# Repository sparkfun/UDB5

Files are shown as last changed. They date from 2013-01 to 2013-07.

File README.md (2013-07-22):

UDB5 - UAV Development Board
===============

[UDB5  
*UDB5 (GPS-11703)*](https://www.sparkfun.com/products/11703)

The UDB5 is the fith generation UAV Development board. The main difference from UDB4 is that we moved to an MPU-6000 for the accelerometer and gyro.

For information on the codebase see the [gentlenav repository](https://code.google.com/p/gentlenav/) on google code. 

Repository Contents
-------------------

* **/hardware** - Eagle PCB layout files

License Information
-------------------

All contents of this repository are released under [Creative Commons Share-alike 3.0](http://creativecommons.org/licenses/by-sa/3.0/).

Authors: Jordan McConnell, Aaron Weiss @ SparkFun Electonics

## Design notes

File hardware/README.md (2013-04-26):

UDB5
====

These are the Eagle CAD files for the UDB5.

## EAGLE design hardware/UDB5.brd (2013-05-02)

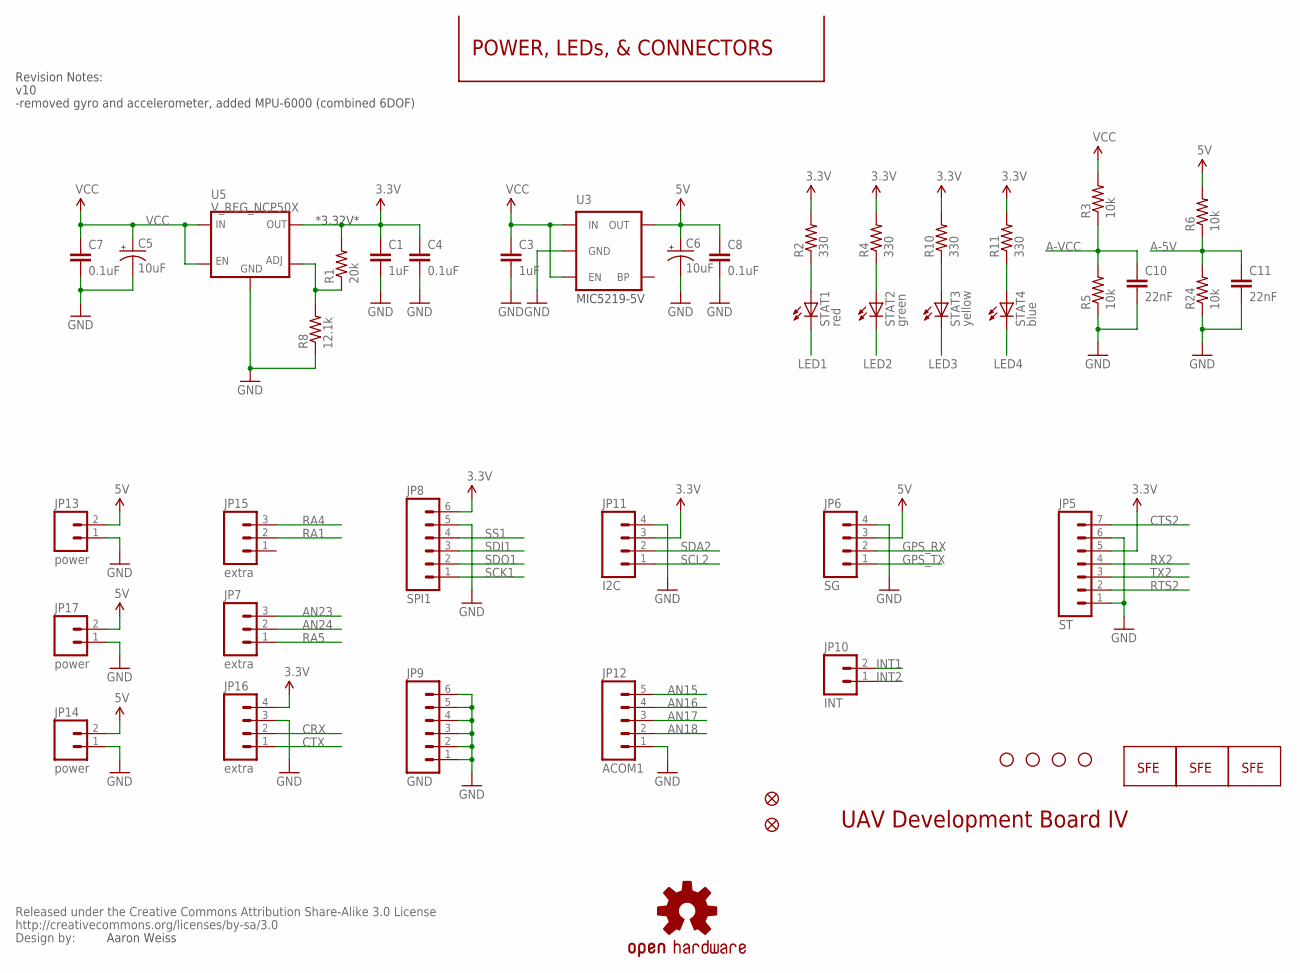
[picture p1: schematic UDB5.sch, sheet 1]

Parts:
C1, C3: 1uF; 0402-CAP
C4, C7, C8: 0.1uF; 0402-CAP
C5, C6: 10uF; EIA3216
C10, C11: 22nF; 0402-CAP
CC_TEXT1: CREATIVE_COMMONS
JP3: LOGO-SFENEW; SFE-NEW-WEBLOGO
JP5: ST; 1X07
JP6: SG; 1X04
JP7, JP15: extra; 1X03
JP8: SPI1; 1X06
JP9: GND; 1X06
JP10: INT; 1X02
JP11: I2C; 1X04
JP12: ACOM1; 1X05
JP13, JP14, JP17: power; 1X02
JP16: extra; 1X04
JP18, JP19: FIDUCIAL1X2.5; FIDUCIAL-1X2.5
LOGO1: LOGO-SFENW2; SFE-NEW-WEB
R1: 20k; 0402-RES
R2, R4, R10, R11: 330; 0402-RES
R3, R5, R6, R24: 10k; 0402-RES
R8: 12.1k; 0402-RES
STAT1: red; LED-0603
STAT2: green; LED-0603
STAT3: yellow; LED-0603
STAT4: blue; LED-0603
U3: V_REG_LDOSMD; SOT23-5
U5: V_REG_NCP50X; DPAK-5
U$2, U$3, U$4, U$5: STAND-OFF
U$9: OSHW-LOGOS; OSHW-LOGO-S
U$10: LOGO-SFESK; SFE-LOGO-FLAME

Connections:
3.3V: C1.1, C4.1, JP5.5, JP8.6, JP11.3, JP16.4, R1.2, R2.2, R4.2, R10.2, R11.2, U5.VOUT (OUT); also elsewhere on the board
5V: C6.A (+), C8.1, JP6.3, JP13.2, JP14.2, JP17.2, R6.2, U3.5 (OUT); also elsewhere on the board
A-5V: C11.1, R6.1, R24.2; also elsewhere on the board
A-VCC: C10.1, R3.1, R5.2; also elsewhere on the board
AN15: JP12.5; also elsewhere on the board
AN16: JP12.4; also elsewhere on the board
AN17: JP12.3; also elsewhere on the board
AN18: JP12.2; also elsewhere on the board
AN23: JP7.3; also elsewhere on the board
AN24: JP7.2; also elsewhere on the board
CRX: JP16.2; also elsewhere on the board
CTS2: JP5.7; also elsewhere on the board
CTX: JP16.1; also elsewhere on the board
GND: C1.2, C3.2, C4.2, C5.C (-), C6.C (-), C7.2, C8.2, C10.2, C11.2, JP5.1, JP5.6, JP6.4, JP8.5, JP9.1, JP9.2, JP9.3, JP9.4, JP9.5, JP9.6, JP11.4, JP12.1, JP13.1, JP14.1, JP16.3, JP17.1, R5.1, R8.1, R24.1, U3.2 (GND), U5.GND; also elsewhere on the board
GPS_RX: JP6.2; also elsewhere on the board
GPS_TX: JP6.1; also elsewhere on the board
INT1: JP10.2; also elsewhere on the board
INT2: JP10.1; also elsewhere on the board
LED1: STAT1.C; also elsewhere on the board
LED2: STAT2.C; also elsewhere on the board
LED3: STAT3.C; also elsewhere on the board
LED4: STAT4.C; also elsewhere on the board
unnamed: R2.1, STAT1.A
unnamed: R4.1, STAT2.A
unnamed: R1.1, R8.2, U5.ADJ
unnamed: R10.1, STAT3.A
unnamed: R11.1, STAT4.A
RA1: JP15.2; also elsewhere on the board
RA4: JP15.3; also elsewhere on the board
RA5: JP7.1; also elsewhere on the board
RTS2: JP5.2; also elsewhere on the board
RX2: JP5.4; also elsewhere on the board
SCK1: JP8.1; also elsewhere on the board
SCL2: JP11.1; also elsewhere on the board
SDA2: JP11.2; also elsewhere on the board
SDI1: JP8.3; also elsewhere on the board
SDO1: JP8.2; also elsewhere on the board
SS1: JP8.4; also elsewhere on the board
TX2: JP5.3; also elsewhere on the board
VCC: C3.1, C5.A (+), C7.1, R3.2, U3.1 (IN), U3.3 (EN), U5.EN, U5.VIN (IN); also elsewhere on the board

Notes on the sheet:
Aaron Weiss
POWER, LEDs, & CONNECTORS
UAV Development Board IV
*3.32V*
MIC5219-5V
v10
-removed gyro and accelerometer, added MPU-6000 (combined 6DOF)
Revision Notes:

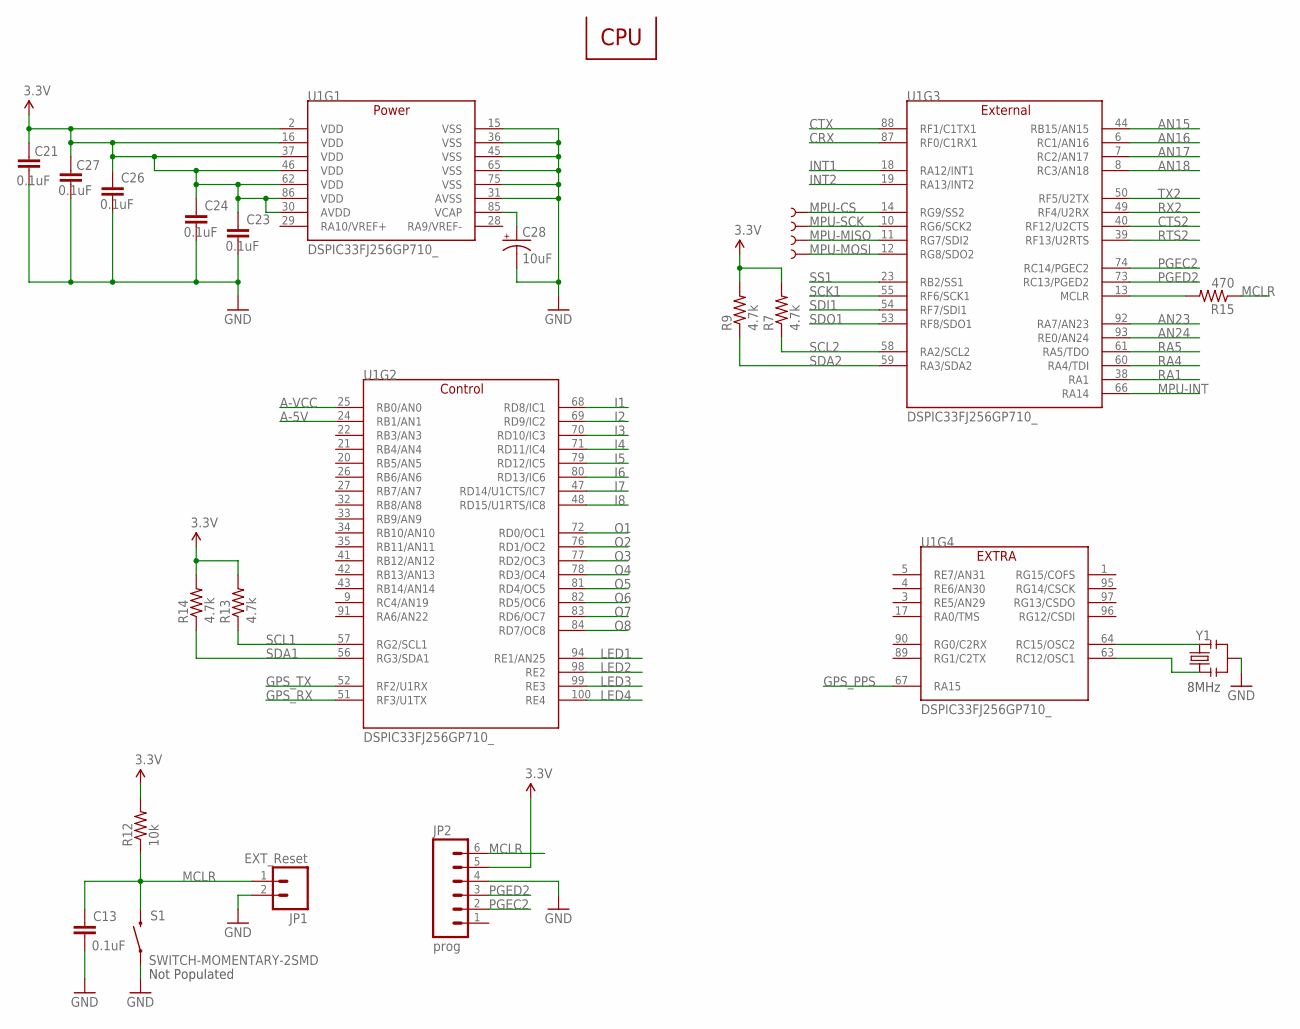
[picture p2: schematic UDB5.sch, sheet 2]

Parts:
C13, C21, C23, C24, C26, C27: 0.1uF; 0402-CAP
C28: 10uF; EIA3216
JP1: EXT_Reset; 1X02
JP2: prog; 1X06
R7, R9, R13, R14: 4.7k; 0402-RES
R12: 10k; 0402-RES
R15: 470; 0402-RES
S1: SWITCH-MOMENTARY-2SMD; TACTILE_SWITCH_SMD
TP1, TP2, TP3, TP4: TEST-POINT3; PAD.03X.03
U1: DSPIC33FJ256GP710_; TQFP-100-12X12MM
Y1: RESONATORSMD; RESONATOR-SMD

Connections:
3.3V: C21.1, C23.1, C24.1, C26.1, C27.1, JP2.5, R7.2, R9.2, R12.2, R13.2, R14.2, U1.2 (VDD), U1.16 (VDD), U1.30 (AVDD), U1.37 (VDD), U1.46 (VDD), U1.62 (VDD), U1.86 (VDD); also elsewhere on the board
A-5V: U1.24 (RB1/AN1); also elsewhere on the board
A-VCC: U1.25 (RB0/AN0); also elsewhere on the board
AN15: U1.44 (RB15/AN15); also elsewhere on the board
AN16: U1.6 (RC1/AN16); also elsewhere on the board
AN17: U1.7 (RC2/AN17); also elsewhere on the board
AN18: U1.8 (RC3/AN18); also elsewhere on the board
AN23: U1.92 (RA7/AN23); also elsewhere on the board
AN24: U1.93 (RE0/AN24); also elsewhere on the board
CRX: U1.87 (RF0/C1RX1); also elsewhere on the board
CTS2: U1.40 (RF12/U2CTS); also elsewhere on the board
CTX: U1.88 (RF1/C1TX1); also elsewhere on the board
GND: C13.2, C21.2, C23.2, C24.2, C26.2, C27.2, C28.C (-), JP1.2, JP2.4, S1.1, U1.15 (VSS), U1.31 (AVSS), U1.36 (VSS), U1.45 (VSS), U1.65 (VSS), U1.75 (VSS), Y1.2; also elsewhere on the board
GPS_PPS: U1.67 (RA15); also elsewhere on the board
GPS_RX: U1.51 (RF3/U1TX); also elsewhere on the board
GPS_TX: U1.52 (RF2/U1RX); also elsewhere on the board
I1: U1.68 (RD8/IC1); also elsewhere on the board
I2: U1.69 (RD9/IC2); also elsewhere on the board
I3: U1.70 (RD10/IC3); also elsewhere on the board
I4: U1.71 (RD11/IC4); also elsewhere on the board
I5: U1.79 (RD12/IC5); also elsewhere on the board
I6: U1.80 (RD13/IC6); also elsewhere on the board
I7: U1.47 (RD14/U1CTS/IC7); also elsewhere on the board
I8: U1.48 (RD15/U1RTS/IC8); also elsewhere on the board
INT1: U1.18 (RA12/INT1); also elsewhere on the board
INT2: U1.19 (RA13/INT2); also elsewhere on the board
LED1: U1.94 (RE1/AN25); also elsewhere on the board
LED2: U1.98 (RE2); also elsewhere on the board
LED3: U1.99 (RE3); also elsewhere on the board
LED4: U1.100 (RE4); also elsewhere on the board
MCLR: C13.1, JP1.1, JP2.6, R12.1, R15.1, S1.3 (2)
MPU-CS: TP1.P$1, U1.14 (RG9/SS2); also elsewhere on the board
MPU-INT: U1.66 (RA14); also elsewhere on the board
MPU-MISO: TP3.P$1, U1.11 (RG7/SDI2); also elsewhere on the board
MPU-MOSI: TP4.P$1, U1.12 (RG8/SDO2); also elsewhere on the board
MPU-SCK: TP2.P$1, U1.10 (RG6/SCK2); also elsewhere on the board
unnamed: U1.64 (RC15/OSC2), Y1.3
unnamed: U1.63 (RC12/OSC1), Y1.1
unnamed: R15.2, U1.13 (MCLR)
unnamed: C28.A (+), U1.85 (VCAP)
O1: U1.72 (RD0/OC1); also elsewhere on the board
O2: U1.76 (RD1/OC2); also elsewhere on the board
O3: U1.77 (RD2/OC3); also elsewhere on the board
O4: U1.78 (RD3/OC4); also elsewhere on the board
O5: U1.81 (RD4/OC5); also elsewhere on the board
O6: U1.82 (RD5/OC6); also elsewhere on the board
O7: U1.83 (RD6/OC7); also elsewhere on the board
O8: U1.84 (RD7/OC8); also elsewhere on the board
PGEC2: JP2.2, U1.74 (RC14/PGEC2)
PGED2: JP2.3, U1.73 (RC13/PGED2)
RA1: U1.38 (RA1); also elsewhere on the board
RA4: U1.60 (RA4/TDI); also elsewhere on the board
RA5: U1.61 (RA5/TDO); also elsewhere on the board
RTS2: U1.39 (RF13/U2RTS); also elsewhere on the board
RX2: U1.49 (RF4/U2RX); also elsewhere on the board
SCK1: U1.55 (RF6/SCK1); also elsewhere on the board
SCL1: R13.1, U1.57 (RG2/SCL1); also elsewhere on the board
SCL2: R7.1, U1.58 (RA2/SCL2); also elsewhere on the board
SDA1: R14.1, U1.56 (RG3/SDA1); also elsewhere on the board
SDA2: R9.1, U1.59 (RA3/SDA2); also elsewhere on the board
SDI1: U1.54 (RF7/SDI1); also elsewhere on the board
SDO1: U1.53 (RF8/SDO1); also elsewhere on the board
SS1: U1.23 (RB2/SS1); also elsewhere on the board
TX2: U1.50 (RF5/U2TX); also elsewhere on the board

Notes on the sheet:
CPU
8MHz
Not Populated

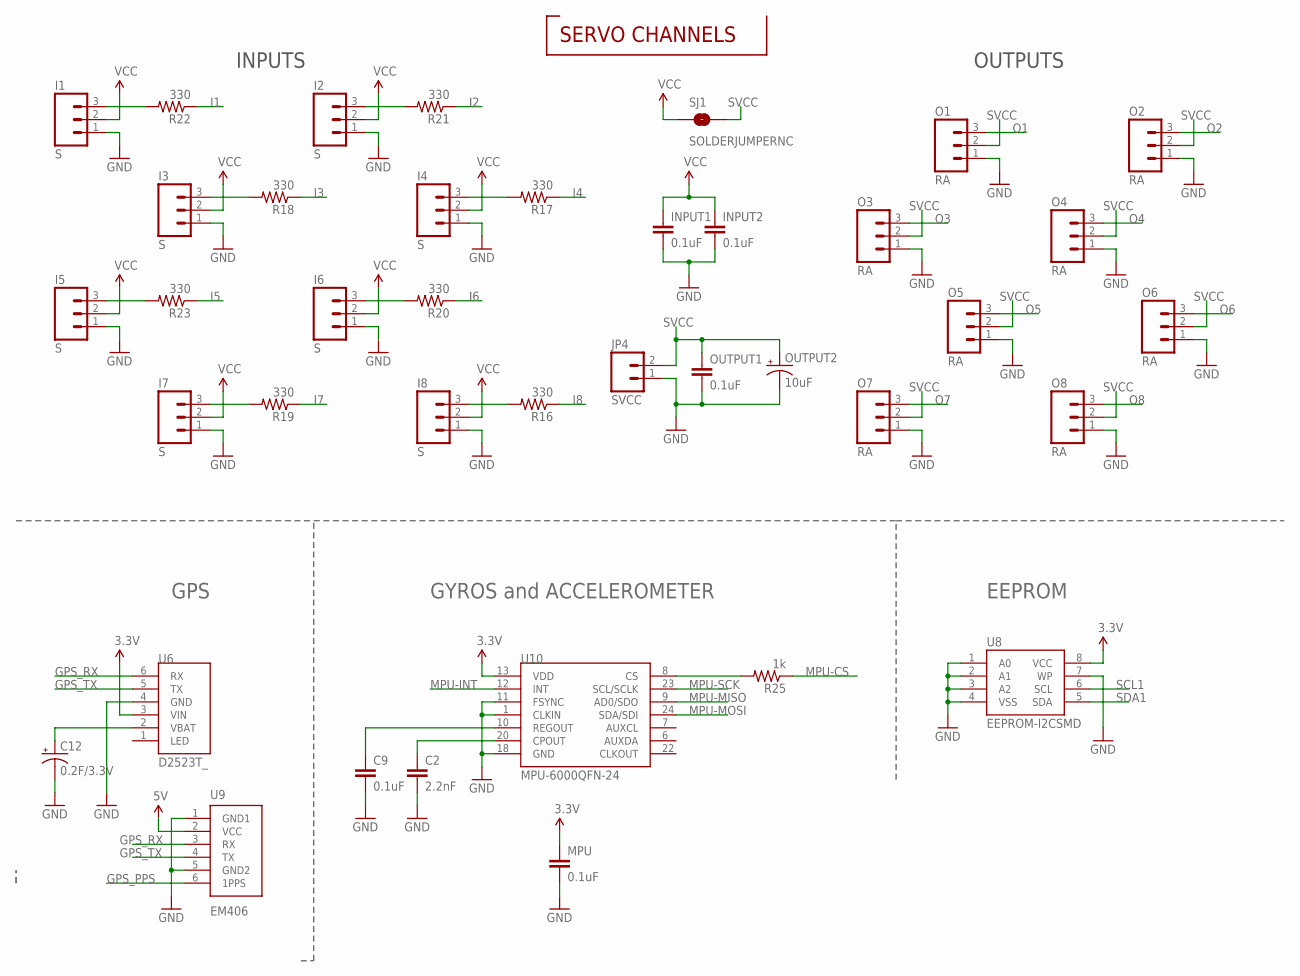
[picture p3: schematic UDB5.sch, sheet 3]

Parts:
C2: 2.2nF; 0402-CAP
C9: 0.1uF; 0402-CAP
C12: 0.2F/3.3V; EN_J2
I1, I2, I3, I4, I5, I6, I7, I8: S; 1X03
INPUT1, INPUT2: 0.1uF; 0402-CAP
JP4: SVCC; 1X02
MPU: 0.1uF; 0402-CAP
O1, O2, O3, O4, O5, O6, O7, O8: RA; 1X03
OUTPUT1: 0.1uF; 0402-CAP
OUTPUT2: 10uF; EIA3216
R16, R17, R18, R19, R20, R21, R22, R23: 330; 0402-RES
R25: 1k; 0402-RES
SJ1: SOLDERJUMPERNC; SJ_2S
U6: D2523T_; EM406
U8: EEPROM-I2CSMD; SO08
U9: EM406
U10: MPU-6000QFN-24; QFN-24-TESTING

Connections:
3.3V: MPU.1, U6.3 (VIN), U8.8 (VCC), U10.13 (VDD); also elsewhere on the board
5V: U9.2 (VCC); also elsewhere on the board
GND: C2.2, C9.2, C12.-, I1.1, I2.1, I3.1, I4.1, I5.1, I6.1, I7.1, I8.1, INPUT1.2, INPUT2.2, JP4.1, MPU.2, O1.1, O2.1, O3.1, O4.1, O5.1, O6.1, O7.1, O8.1, OUTPUT1.2, OUTPUT2.C (-), U6.4 (GND), U8.1 (A0), U8.2 (A1), U8.3 (A2), U8.4 (VSS), U8.7 (WP), U9.1 (GND1), U9.5 (GND2), U10.1 (CLKIN), U10.11 (FSYNC), U10.18 (GND); also elsewhere on the board
GPS_PPS: U9.6 (1PPS); also elsewhere on the board
GPS_RX: U6.6 (RX), U9.3 (RX); also elsewhere on the board
GPS_TX: U6.5 (TX), U9.4 (TX); also elsewhere on the board
I1: R22.1; also elsewhere on the board
I2: R21.1; also elsewhere on the board
I3: R18.1; also elsewhere on the board
I4: R17.1; also elsewhere on the board
I5: R23.1; also elsewhere on the board
I6: R20.1; also elsewhere on the board
I7: R19.1; also elsewhere on the board
I8: R16.1; also elsewhere on the board
MPU-CS: R25.1; also elsewhere on the board
MPU-INT: U10.12 (INT); also elsewhere on the board
MPU-MISO: U10.9 (AD0/SDO); also elsewhere on the board
MPU-MOSI: U10.24 (SDA/SDI); also elsewhere on the board
MPU-SCK: U10.23 (SCL/SCLK); also elsewhere on the board
unnamed: C12.+, U6.2 (VBAT)
unnamed: R25.2, U10.8 (CS)
unnamed: C2.1, U10.20 (CPOUT)
unnamed: I8.3, R16.2
unnamed: I4.3, R17.2
unnamed: C9.1, U10.10 (REGOUT)
unnamed: I3.3, R18.2
unnamed: I7.3, R19.2
unnamed: I6.3, R20.2
unnamed: I2.3, R21.2
unnamed: I1.3, R22.2
unnamed: I5.3, R23.2
O1: O1.3; also elsewhere on the board
O2: O2.3; also elsewhere on the board
O3: O3.3; also elsewhere on the board
O4: O4.3; also elsewhere on the board
O5: O5.3; also elsewhere on the board
O6: O6.3; also elsewhere on the board
O7: O7.3; also elsewhere on the board
O8: O8.3; also elsewhere on the board
SCL1: U8.6 (SCL); also elsewhere on the board
SDA1: U8.5 (SDA); also elsewhere on the board
SVCC: JP4.2, O1.2, O2.2, O3.2, O4.2, O5.2, O6.2, O7.2, O8.2, OUTPUT1.1, OUTPUT2.A (+), SJ1.2
VCC: I1.2, I2.2, I3.2, I4.2, I5.2, I6.2, I7.2, I8.2, INPUT1.1, INPUT2.1, SJ1.1; also elsewhere on the board

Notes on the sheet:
INPUTS
OUTPUTS
SERVO CHANNELS
GPS
EEPROM
GYROS and ACCELEROMETER

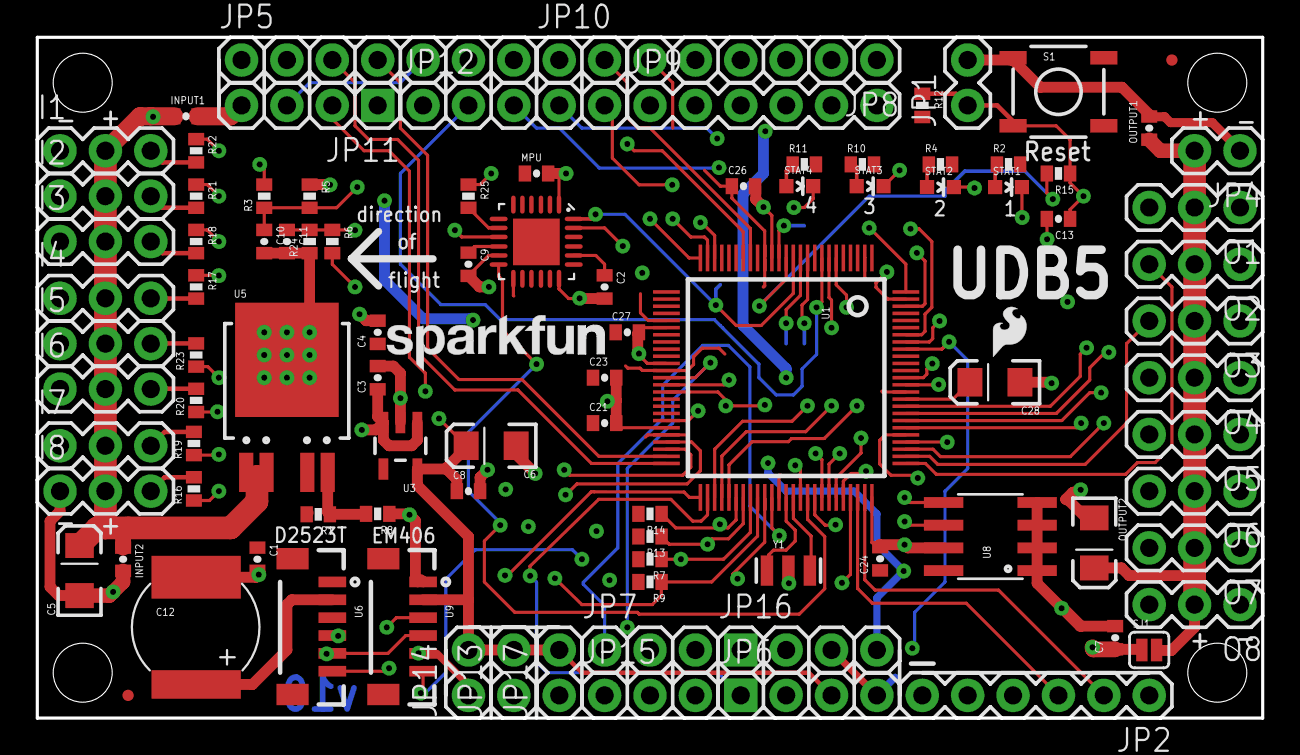
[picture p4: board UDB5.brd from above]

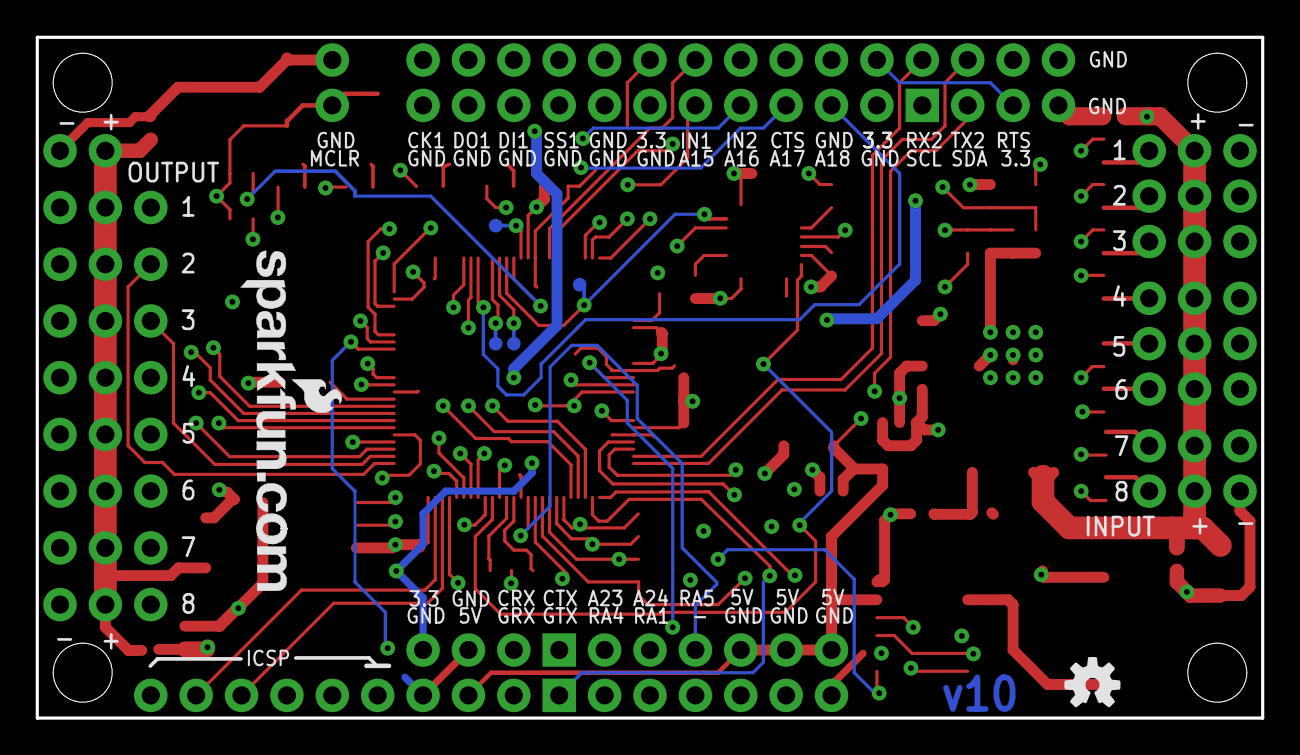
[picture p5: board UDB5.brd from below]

Board: 4 copper layers, 68.6 x 38.1 mm, 110 parts (6 on the bottom side), 84 nets.

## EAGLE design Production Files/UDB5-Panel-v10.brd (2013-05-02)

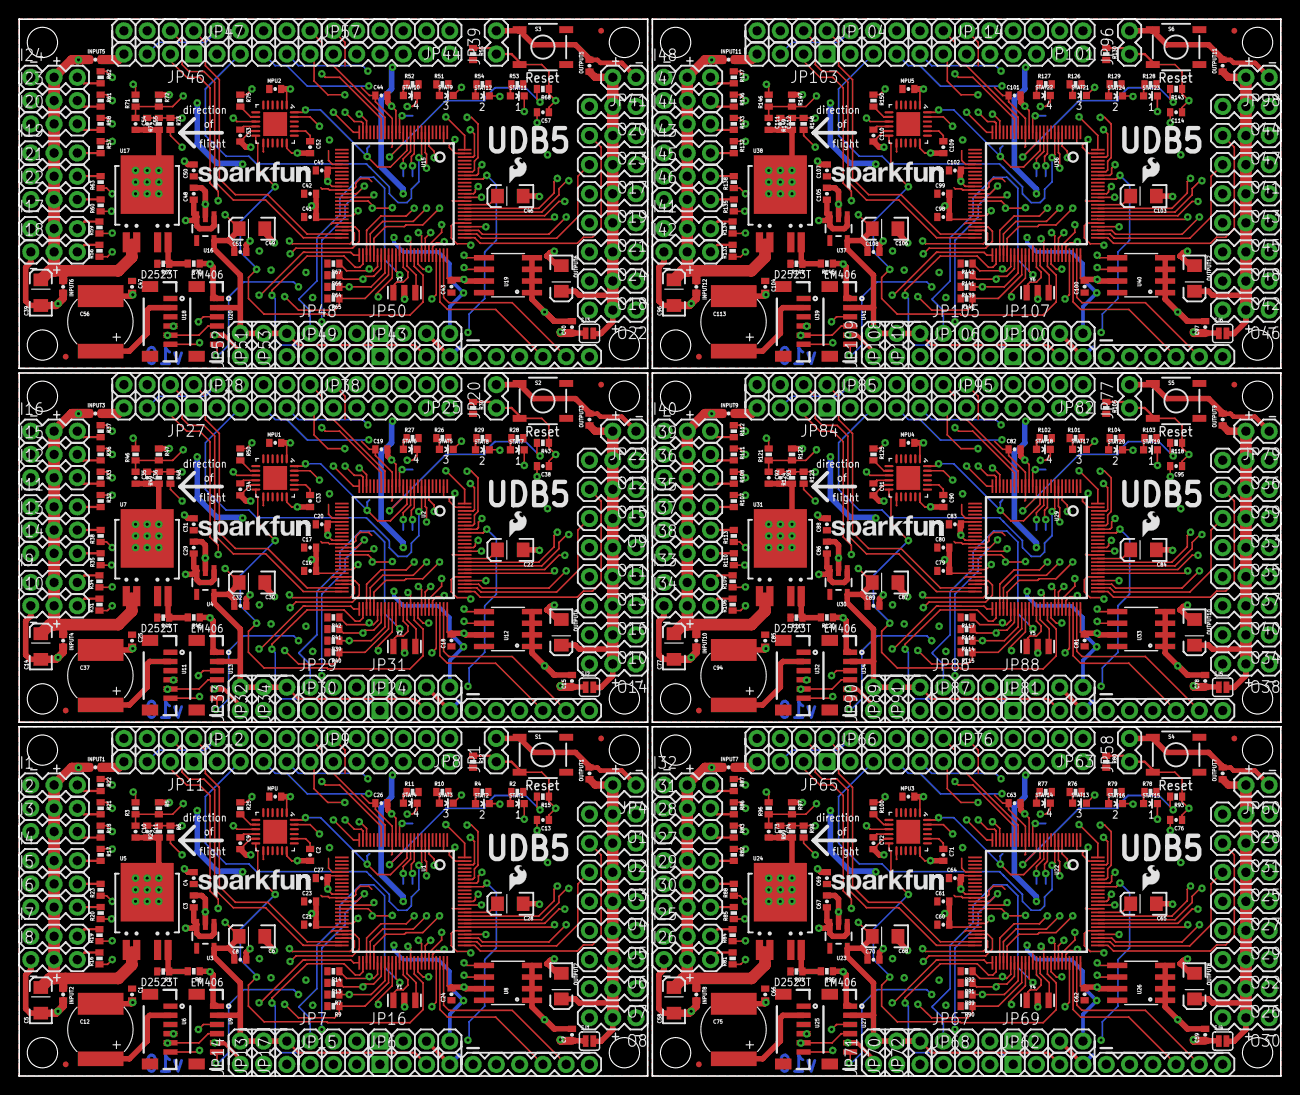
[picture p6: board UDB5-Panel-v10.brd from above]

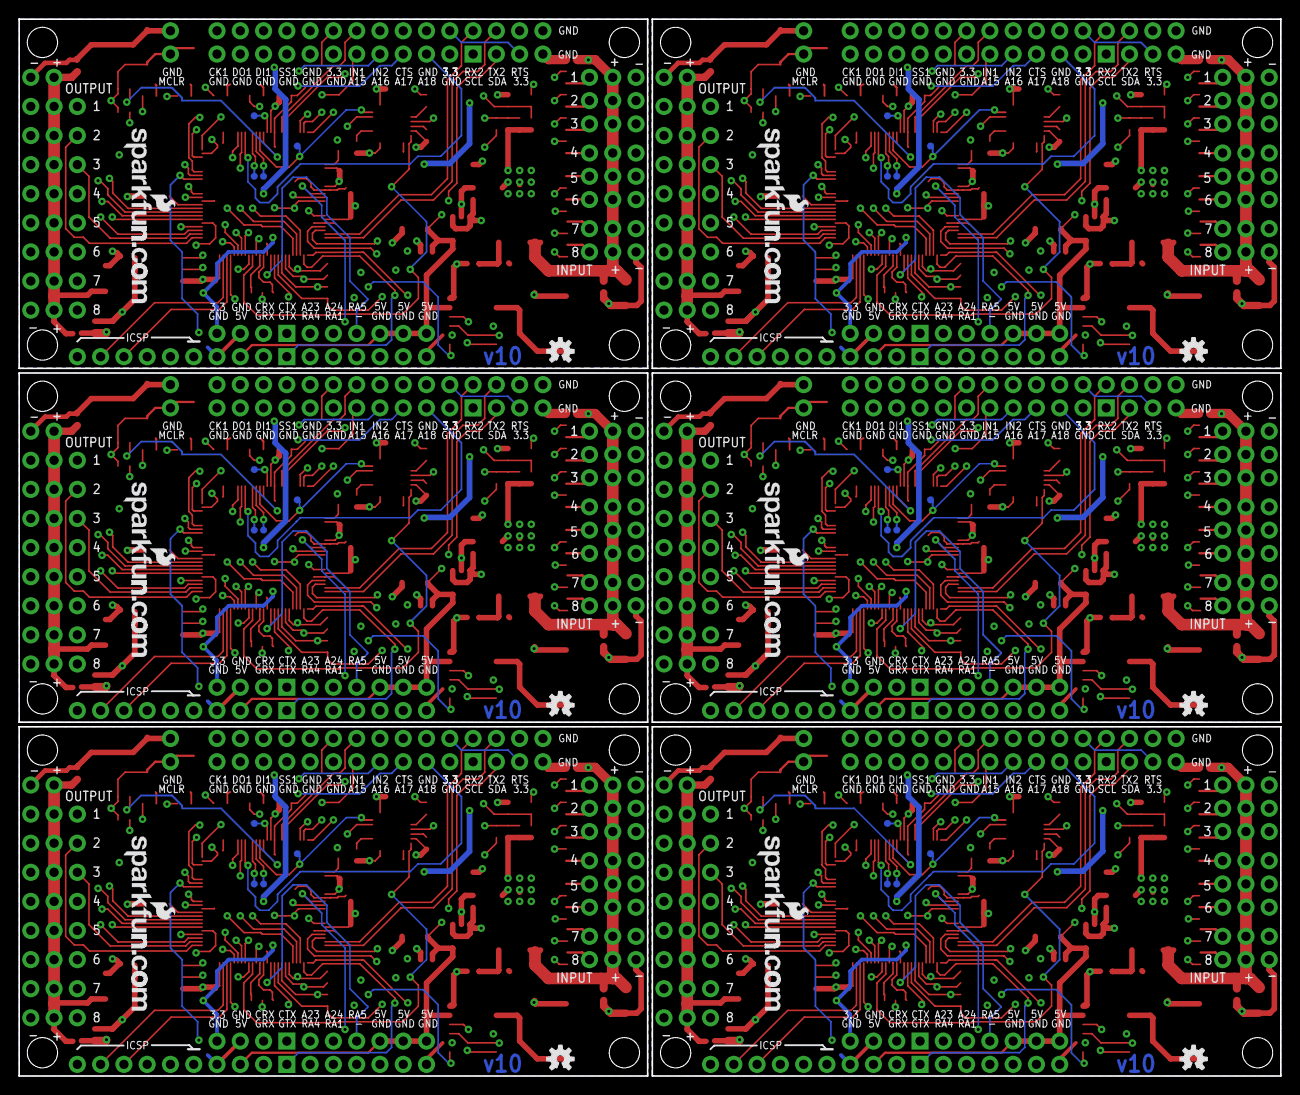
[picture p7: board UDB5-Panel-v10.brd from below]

Board: 4 copper layers, 137.7 x 115.3 mm, 654 parts (36 on the bottom side), 504 nets.

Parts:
C1, C3, C25, C29, C47, C48, C66, C67, C85, C86, C104, C105: 1uF; 0402-CAP
C2, C33, C52, C71, C90, C109: 2.2nF; 0402-CAP
C4, C7, C8, C9, C13, C15, C16, C17, C18, C19, C20, C21, C23, C24, C26, C27, C31, C32, C34, C38, C40, C41, C42, C43, C44, C45, C50, C51, C53, C57, C59, C60, C61, C62, C63, C64, C69, C70, C72, C76, C78, C79, C80, C81, C82, C83, C88, C89, C91, C95, C97, C98, C99, C100, C101, C102, C107, C108, C110, C114: 0.1uF; 0402-CAP
C5, C6, C14, C22, C28, C30, C39, C46, C49, C58, C65, C68, C77, C84, C87, C96, C103, C106: 10uF; EIA3216
C10, C11, C35, C36, C54, C55, C73, C74, C92, C93, C111, C112: 22nF; 0402-CAP
C12, C37, C56, C75, C94, C113: 0.2F/3.3V; EN_J2
I1, I2, I3, I4, I5, I6, I7, I8, I9, I10, I11, I12, I13, I14, I15, I16, I17, I18, I19, I20, I21, I22, I23, I24, I25, I26, I27, I28, I29, I30, I31, I32, I33, I34, I35, I36, I37, I38, I39, I40, I41, I42, I43, I44, I45, I46, I47, I48: S; 1X03
INPUT1, INPUT2, INPUT3, INPUT4, INPUT5, INPUT6, INPUT7, INPUT8, INPUT9, INPUT10, INPUT11, INPUT12: 0.1uF; 0402-CAP
JP1, JP20, JP39, JP58, JP77, JP96: EXT_Reset; 1X02
JP2, JP21, JP40, JP59, JP78, JP97: prog; 1X06
JP3, JP35, JP54, JP73, JP92, JP111: LOGO-SFENEW; SFE-NEW-WEBLOGO
JP4, JP22, JP41, JP60, JP79, JP98: SVCC; 1X02
JP5, JP23, JP42, JP61, JP80, JP99: ST; 1X07
JP6, JP24, JP43, JP62, JP81, JP100: SG; 1X04
JP7, JP15, JP29, JP30, JP48, JP49, JP67, JP68, JP86, JP87, JP105, JP106: extra; 1X03
JP8, JP25, JP44, JP63, JP82, JP101: SPI1; 1X06
JP9, JP38, JP57, JP76, JP95, JP114: GND; 1X06
JP10, JP26, JP45, JP64, JP83, JP102: INT; 1X02
JP11, JP27, JP46, JP65, JP84, JP103: I2C; 1X04
JP12, JP28, JP47, JP66, JP85, JP104: ACOM1; 1X05
JP13, JP14, JP17, JP32, JP33, JP34, JP51, JP52, JP53, JP70, JP71, JP72, JP89, JP90, JP91, JP108, JP109, JP110: power; 1X02
JP16, JP31, JP50, JP69, JP88, JP107: extra; 1X04
JP18, JP19, JP36, JP37, JP55, JP56, JP74, JP75, JP93, JP94, JP112, JP113: FIDUCIAL1X2.5; FIDUCIAL-1X2.5
LOGO1, LOGO2, LOGO3, LOGO4, LOGO5, LOGO6: LOGO-SFENW2; SFE-NEW-WEB
MPU, MPU1, MPU2, MPU3, MPU4, MPU5: 0.1uF; 0402-CAP
O1, O2, O3, O4, O5, O6, O7, O8, O9, O10, O11, O12, O13, O14, O15, O16, O17, O18, O19, O20, O21, O22, O23, O24, O25, O26, O27, O28, O29, O30, O31, O32, O33, O34, O35, O36, O37, O38, O39, O40, O41, O42, O43, O44, O45, O46, O47, O48: RA; 1X03
OUTPUT1, OUTPUT3, OUTPUT5, OUTPUT7, OUTPUT9, OUTPUT11: 0.1uF; 0402-CAP
OUTPUT2, OUTPUT4, OUTPUT6, OUTPUT8, OUTPUT10, OUTPUT12: 10uF; EIA3216
R1, R44, R69, R94, R119, R144: 20k; 0402-RES
R2, R4, R10, R11, R16, R17, R18, R19, R20, R21, R22, R23, R26, R27, R28, R29, R31, R32, R33, R34, R35, R36, R37, R38, R51, R52, R53, R54, R56, R57, R58, R59, R60, R61, R62, R63, R76, R77, R78, R79, R81, R82, R83, R84, R85, R86, R87, R88, R101, R102, R103, R104, R106, R107, R108, R109, R110, R111, R112, R113, R126, R127, R128, R129, R131, R132, R133, R134, R135, R136, R137, R138: 330; 0402-RES
R3, R5, R6, R12, R24, R30, R46, R47, R48, R49, R55, R71, R72, R73, R74, R80, R96, R97, R98, R99, R105, R121, R122, R123, R124, R130, R146, R147, R148, R149: 10k; 0402-RES
R7, R9, R13, R14, R39, R40, R41, R42, R64, R65, R66, R67, R89, R90, R91, R92, R114, R115, R116, R117, R139, R140, R141, R142: 4.7k; 0402-RES
R8, R45, R70, R95, R120, R145: 12.1k; 0402-RES
R15, R43, R68, R93, R118, R143: 470; 0402-RES
R25, R50, R75, R100, R125, R150: 1k; 0402-RES
S1, S2, S3, S4, S5, S6: SWITCH-MOMENTARY-2SMD; TACTILE_SWITCH_SMD
SJ1, SJ2, SJ3, SJ4, SJ5, SJ6: SOLDERJUMPERNC; SJ_2S
STAT1, STAT7, STAT11, STAT15, STAT19, STAT23: red; LED-0603
STAT2, STAT8, STAT12, STAT16, STAT20, STAT24: green; LED-0603
STAT3, STAT5, STAT9, STAT13, STAT17, STAT21: yellow; LED-0603
STAT4, STAT6, STAT10, STAT14, STAT18, STAT22: blue; LED-0603
TP1, TP2, TP3, TP4, TP5, TP6, TP7, TP8, TP9, TP10, TP11, TP12, TP13, TP14, TP15, TP16, TP17, TP18, TP19, TP20, TP21, TP22, TP23, TP24: TEST-POINT3; PAD.03X.03
U1, U2, U15, U22, U29, U36: DSPIC33FJ256GP710_; TQFP-100-12X12MM
U3, U4, U16, U23, U30, U37: V_REG_LDOSMD; SOT23-5
U5, U7, U17, U24, U31, U38: V_REG_NCP50X; DPAK-5
U6, U11, U18, U25, U32, U39: D2523T_; EM406
U8, U12, U19, U26, U33, U40: EEPROM-I2CSMD; SO08
U9, U13, U20, U27, U34, U41: EM406
U10, U14, U21, U28, U35, U42: MPU-6000QFN-24; QFN-24-TESTING
U$1, U$2, U$3, U$4, U$5, U$6, U$7, U$8, U$13, U$14, U$15, U$16, U$19, U$20, U$21, U$22, U$25, U$26, U$27, U$28, U$31, U$32, U$33, U$34: STAND-OFF
U$9, U$12, U$18, U$24, U$30, U$36: OSHW-LOGOS; OSHW-LOGO-S
U$10, U$11, U$17, U$23, U$29, U$35: LOGO-SFESK; SFE-LOGO-FLAME
Y1, Y2, Y3, Y4, Y5, Y6: RESONATORSMD; RESONATOR-SMD

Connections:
3.3V: C1.1, C4.1, C21.1, C23.1, C24.1, C26.1, C27.1, JP2.5, JP5.5, JP8.6, JP11.3, JP16.4, MPU.1, R1.2, R2.2, R4.2, R7.2, R9.2, R10.2, R11.2, R12.2, R13.2, R14.2, U1.2, U1.16, U1.30, U1.37, U1.46, U1.62, U1.86, U5.VOUT, U6.3, U8.8, U10.13
3.3V1: C16.1, C17.1, C18.1, C19.1, C20.1, C25.1, C31.1, JP21.5, JP23.5, JP25.6, JP27.3, JP31.4, MPU1.1, R26.2, R27.2, R28.2, R29.2, R30.2, R39.2, R40.2, R41.2, R42.2, R44.2, U2.2, U2.16, U2.30, U2.37, U2.46, U2.62, U2.86, U7.VOUT, U11.3, U12.8, U14.13
3.3V2: C41.1, C42.1, C43.1, C44.1, C45.1, C47.1, C50.1, JP40.5, JP42.5, JP44.6, JP46.3, JP50.4, MPU2.1, R51.2, R52.2, R53.2, R54.2, R55.2, R64.2, R65.2, R66.2, R67.2, R69.2, U15.2, U15.16, U15.30, U15.37, U15.46, U15.62, U15.86, U17.VOUT, U18.3, U19.8, U21.13
3.3V3: C60.1, C61.1, C62.1, C63.1, C64.1, C66.1, C69.1, JP59.5, JP61.5, JP63.6, JP65.3, JP69.4, MPU3.1, R76.2, R77.2, R78.2, R79.2, R80.2, R89.2, R90.2, R91.2, R92.2, R94.2, U22.2, U22.16, U22.30, U22.37, U22.46, U22.62, U22.86, U24.VOUT, U25.3, U26.8, U28.13
3.3V4: C79.1, C80.1, C81.1, C82.1, C83.1, C85.1, C88.1, JP78.5, JP80.5, JP82.6, JP84.3, JP88.4, MPU4.1, R101.2, R102.2, R103.2, R104.2, R105.2, R114.2, R115.2, R116.2, R117.2, R119.2, U29.2, U29.16, U29.30, U29.37, U29.46, U29.62, U29.86, U31.VOUT, U32.3, U33.8, U35.13
3.3V5: C98.1, C99.1, C100.1, C101.1, C102.1, C104.1, C107.1, JP97.5, JP99.5, JP101.6, JP103.3, JP107.4, MPU5.1, R126.2, R127.2, R128.2, R129.2, R130.2, R139.2, R140.2, R141.2, R142.2, R144.2, U36.2, U36.16, U36.30, U36.37, U36.46, U36.62, U36.86, U38.VOUT, U39.3, U40.8, U42.13
5V: C6.A, C8.1, JP6.3, JP13.2, JP14.2, JP17.2, R6.2, U3.5, U9.2
5V1: C30.A, C32.1, JP24.3, JP32.2, JP33.2, JP34.2, R48.2, U4.5, U13.2
5V2: C49.A, C51.1, JP43.3, JP51.2, JP52.2, JP53.2, R73.2, U16.5, U20.2
5V3: C68.A, C70.1, JP62.3, JP70.2, JP71.2, JP72.2, R98.2, U23.5, U27.2
5V4: C87.A, C89.1, JP81.3, JP89.2, JP90.2, JP91.2, R123.2, U30.5, U34.2
5V5: C106.A, C108.1, JP100.3, JP108.2, JP109.2, JP110.2, R148.2, U37.5, U41.2
A-5V: C11.1, R6.1, R24.2, U1.24
A-5V1: C36.1, R48.1, R49.2, U2.24
A-5V2: C55.1, R73.1, R74.2, U15.24
A-5V3: C74.1, R98.1, R99.2, U22.24
A-5V4: C93.1, R123.1, R124.2, U29.24
A-5V5: C112.1, R148.1, R149.2, U36.24
A-VCC: C10.1, R3.1, R5.2, U1.25
A-VCC1: C35.1, R46.1, R47.2, U2.25
A-VCC2: C54.1, R71.1, R72.2, U15.25
A-VCC3: C73.1, R96.1, R97.2, U22.25
A-VCC4: C92.1, R121.1, R122.2, U29.25
A-VCC5: C111.1, R146.1, R147.2, U36.25
AN1: JP28.5, U2.44
AN2: JP28.4, U2.6
AN3: JP28.3, U2.7
AN4: JP29.2, U2.93
AN5: JP28.2, U2.8
AN6: JP29.3, U2.92
AN7: JP47.5, U15.44
AN8: JP47.4, U15.6
AN9: JP47.3, U15.7
AN10: JP48.2, U15.93
AN11: JP47.2, U15.8
AN12: JP48.3, U15.92
AN13: JP66.5, U22.44
AN14: JP66.4, U22.6
AN15: JP12.5, U1.44
AN16: JP12.4, U1.6
AN17: JP12.3, U1.7
AN18: JP12.2, U1.8
AN19: JP66.3, U22.7
AN20: JP67.2, U22.93
AN21: JP66.2, U22.8
AN22: JP67.3, U22.92
AN23: JP7.3, U1.92
AN24: JP7.2, U1.93
AN25: JP85.5, U29.44
AN26: JP85.4, U29.6
AN27: JP85.3, U29.7
AN28: JP86.2, U29.93
AN29: JP85.2, U29.8
AN30: JP86.3, U29.92
AN31: JP104.5, U36.44
AN32: JP104.4, U36.6
AN33: JP104.3, U36.7
AN34: JP105.2, U36.93
AN35: JP104.2, U36.8
AN36: JP105.3, U36.92
CRX: JP16.2, U1.87
CRX1: JP31.2, U2.87
CRX2: JP50.2, U15.87
CRX3: JP69.2, U22.87
CRX4: JP88.2, U29.87
CRX5: JP107.2, U36.87
CTS1: JP23.7, U2.40
CTS2: JP5.7, U1.40
CTS3: JP42.7, U15.40
CTS4: JP61.7, U22.40
CTS5: JP80.7, U29.40
CTS6: JP99.7, U36.40
CTX: JP16.1, U1.88
CTX1: JP31.1, U2.88
CTX2: JP50.1, U15.88
CTX3: JP69.1, U22.88
CTX4: JP88.1, U29.88
CTX5: JP107.1, U36.88
GND: C1.2, C2.2, C3.2, C4.2, C5.C, C6.C, C7.2, C8.2, C9.2, C10.2, C11.2, C12.-, C13.2, C21.2, C23.2, C24.2, C26.2, C27.2, C28.C, I1.1, I2.1, I3.1, I4.1, I5.1, I6.1, I7.1, I8.1, INPUT1.2, INPUT2.2, JP1.2, JP2.4, JP4.1, JP5.1, JP5.6, JP6.4, JP8.5, JP9.1, JP9.2, JP9.3, JP9.4, JP9.5, JP9.6, JP11.4, JP12.1, JP13.1, JP14.1, JP16.3, JP17.1, MPU.2, O1.1, O2.1, O3.1, O4.1, O5.1, O6.1, O7.1, O8.1, OUTPUT1.2, OUTPUT2.C, R5.1, R8.1, R24.1, S1.1, U1.15, U1.31, U1.36, U1.45, U1.65, U1.75, U3.2, U5.GND, U6.4, U8.1, U8.2, U8.3, U8.4, U8.7, U9.1, U9.5, U10.1, U10.11, U10.18, Y1.2
GND1: C14.C, C15.2, C16.2, C17.2, C18.2, C19.2, C20.2, C22.C, C25.2, C29.2, C30.C, C31.2, C32.2, C33.2, C34.2, C35.2, C36.2, C37.-, C38.2, I9.1, I10.1, I11.1, I12.1, I13.1, I14.1, I15.1, I16.1, INPUT3.2, INPUT4.2, JP20.2, JP21.4, JP22.1, JP23.1, JP23.6, JP24.4, JP25.5, JP27.4, JP28.1, JP31.3, JP32.1, JP33.1, JP34.1, JP38.1, JP38.2, JP38.3, JP38.4, JP38.5, JP38.6, MPU1.2, O9.1, O10.1, O11.1, O12.1, O13.1, O14.1, O15.1, O16.1, OUTPUT3.2, OUTPUT4.C, R45.1, R47.1, R49.1, S2.1, U2.15, U2.31, U2.36, U2.45, U2.65, U2.75, U4.2, U7.GND, U11.4, U12.1, U12.2, U12.3, U12.4, U12.7, U13.1, U13.5, U14.1, U14.11, U14.18, Y2.2
GND2: C39.C, C40.2, C41.2, C42.2, C43.2, C44.2, C45.2, C46.C, C47.2, C48.2, C49.C, C50.2, C51.2, C52.2, C53.2, C54.2, C55.2, C56.-, C57.2, I17.1, I18.1, I19.1, I20.1, I21.1, I22.1, I23.1, I24.1, INPUT5.2, INPUT6.2, JP39.2, JP40.4, JP41.1, JP42.1, JP42.6, JP43.4, JP44.5, JP46.4, JP47.1, JP50.3, JP51.1, JP52.1, JP53.1, JP57.1, JP57.2, JP57.3, JP57.4, JP57.5, JP57.6, MPU2.2, O17.1, O18.1, O19.1, O20.1, O21.1, O22.1, O23.1, O24.1, OUTPUT5.2, OUTPUT6.C, R70.1, R72.1, R74.1, S3.1, U15.15, U15.31, U15.36, U15.45, U15.65, U15.75, U16.2, U17.GND, U18.4, U19.1, U19.2, U19.3, U19.4, U19.7, U20.1, U20.5, U21.1, U21.11, U21.18, Y3.2
GND3: C58.C, C59.2, C60.2, C61.2, C62.2, C63.2, C64.2, C65.C, C66.2, C67.2, C68.C, C69.2, C70.2, C71.2, C72.2, C73.2, C74.2, C75.-, C76.2, I25.1, I26.1, I27.1, I28.1, I29.1, I30.1, I31.1, I32.1, INPUT7.2, INPUT8.2, JP58.2, JP59.4, JP60.1, JP61.1, JP61.6, JP62.4, JP63.5, JP65.4, JP66.1, JP69.3, JP70.1, JP71.1, JP72.1, JP76.1, JP76.2, JP76.3, JP76.4, JP76.5, JP76.6, MPU3.2, O25.1, O26.1, O27.1, O28.1, O29.1, O30.1, O31.1, O32.1, OUTPUT7.2, OUTPUT8.C, R95.1, R97.1, R99.1, S4.1, U22.15, U22.31, U22.36, U22.45, U22.65, U22.75, U23.2, U24.GND, U25.4, U26.1, U26.2, U26.3, U26.4, U26.7, U27.1, U27.5, U28.1, U28.11, U28.18, Y4.2
GND4: C77.C, C78.2, C79.2, C80.2, C81.2, C82.2, C83.2, C84.C, C85.2, C86.2, C87.C, C88.2, C89.2, C90.2, C91.2, C92.2, C93.2, C94.-, C95.2, I33.1, I34.1, I35.1, I36.1, I37.1, I38.1, I39.1, I40.1, INPUT9.2, INPUT10.2, JP77.2, JP78.4, JP79.1, JP80.1, JP80.6, JP81.4, JP82.5, JP84.4, JP85.1, JP88.3, JP89.1, JP90.1, JP91.1, JP95.1, JP95.2, JP95.3, JP95.4, JP95.5, JP95.6, MPU4.2, O33.1, O34.1, O35.1, O36.1, O37.1, O38.1, O39.1, O40.1, OUTPUT9.2, OUTPUT10.C, R120.1, R122.1, R124.1, S5.1, U29.15, U29.31, U29.36, U29.45, U29.65, U29.75, U30.2, U31.GND, U32.4, U33.1, U33.2, U33.3, U33.4, U33.7, U34.1, U34.5, U35.1, U35.11, U35.18, Y5.2
GND5: C96.C, C97.2, C98.2, C99.2, C100.2, C101.2, C102.2, C103.C, C104.2, C105.2, C106.C, C107.2, C108.2, C109.2, C110.2, C111.2, C112.2, C113.-, C114.2, I41.1, I42.1, I43.1, I44.1, I45.1, I46.1, I47.1, I48.1, INPUT11.2, INPUT12.2, JP96.2, JP97.4, JP98.1, JP99.1, JP99.6, JP100.4, JP101.5, JP103.4, JP104.1, JP107.3, JP108.1, JP109.1, JP110.1, JP114.1, JP114.2, JP114.3, JP114.4, JP114.5, JP114.6, MPU5.2, O41.1, O42.1, O43.1, O44.1, O45.1, O46.1, O47.1, O48.1, OUTPUT11.2, OUTPUT12.C, R145.1, R147.1, R149.1, S6.1, U36.15, U36.31, U36.36, U36.45, U36.65, U36.75, U37.2, U38.GND, U39.4, U40.1, U40.2, U40.3, U40.4, U40.7, U41.1, U41.5, U42.1, U42.11, U42.18, Y6.2
GPS_PPS: U1.67, U9.6
GPS_PPS1: U2.67, U13.6
GPS_PPS2: U15.67, U20.6
GPS_PPS3: U22.67, U27.6
GPS_PPS4: U29.67, U34.6
GPS_PPS5: U36.67, U41.6
GPS_RX: JP6.2, U1.51, U6.6, U9.3
GPS_RX1: JP24.2, U2.51, U11.6, U13.3
GPS_RX2: JP43.2, U15.51, U18.6, U20.3
GPS_RX3: JP62.2, U22.51, U25.6, U27.3
GPS_RX4: JP81.2, U29.51, U32.6, U34.3
GPS_RX5: JP100.2, U36.51, U39.6, U41.3
GPS_TX: JP6.1, U1.52, U6.5, U9.4
GPS_TX1: JP24.1, U2.52, U11.5, U13.4
GPS_TX2: JP43.1, U15.52, U18.5, U20.4
GPS_TX3: JP62.1, U22.52, U25.5, U27.4
GPS_TX4: JP81.1, U29.52, U32.5, U34.4
GPS_TX5: JP100.1, U36.52, U39.5, U41.4
I1: R22.1, U1.68
I2: R21.1, U1.69
I3: R18.1, U1.70
I4: R17.1, U1.71
I5: R23.1, U1.79
I6: R20.1, U1.80
I7: R19.1, U1.47
I8: R16.1, U1.48
I9: R37.1, U2.68
I10: R36.1, U2.69
I11: R33.1, U2.70
I12: R32.1, U2.71
I13: R38.1, U2.79
I14: R35.1, U2.80
I15: R34.1, U2.47
I16: R31.1, U2.48
I17: R62.1, U15.68
I18: R61.1, U15.69
I19: R58.1, U15.70
I20: R57.1, U15.71
I21: R63.1, U15.79
I22: R60.1, U15.80
I23: R59.1, U15.47
I24: R56.1, U15.48
I25: R87.1, U22.68
I26: R86.1, U22.69
I27: R83.1, U22.70
I28: R82.1, U22.71
I29: R88.1, U22.79
I30: R85.1, U22.80
I31: R84.1, U22.47
I32: R81.1, U22.48
I33: R112.1, U29.68
I34: R111.1, U29.69
I35: R108.1, U29.70
I36: R107.1, U29.71
I37: R113.1, U29.79
I38: R110.1, U29.80
I39: R109.1, U29.47
I40: R106.1, U29.48
I41: R137.1, U36.68
I42: R136.1, U36.69
I43: R133.1, U36.70
I44: R132.1, U36.71
I45: R138.1, U36.79
I46: R135.1, U36.80
I47: R134.1, U36.47
I48: R131.1, U36.48
INT1: JP10.2, U1.18
INT2: JP10.1, U1.19
INT3: JP26.2, U2.18
INT4: JP26.1, U2.19
INT5: JP45.2, U15.18
INT6: JP45.1, U15.19
INT7: JP64.2, U22.18
INT8: JP64.1, U22.19
INT9: JP83.2, U29.18
INT10: JP83.1, U29.19
INT11: JP102.2, U36.18
INT12: JP102.1, U36.19
LED1: STAT1.C, U1.94
LED2: STAT2.C, U1.98
LED3: STAT3.C, U1.99
LED4: STAT4.C, U1.100
LED5: STAT7.C, U2.94
LED6: STAT8.C, U2.98
LED7: STAT5.C, U2.99
LED8: STAT6.C, U2.100
LED9: STAT11.C, U15.94
LED10: STAT12.C, U15.98
LED11: STAT9.C, U15.99
LED12: STAT10.C, U15.100
LED13: STAT15.C, U22.94
LED14: STAT16.C, U22.98
LED15: STAT13.C, U22.99
LED16: STAT14.C, U22.100
LED17: STAT19.C, U29.94
LED18: STAT20.C, U29.98
LED19: STAT17.C, U29.99
LED20: STAT18.C, U29.100
LED21: STAT23.C, U36.94
LED22: STAT24.C, U36.98
LED23: STAT21.C, U36.99
LED24: STAT22.C, U36.100
MCLR: C13.1, JP1.1, JP2.6, R12.1, R15.1, S1.3
MCLR1: C38.1, JP20.1, JP21.6, R30.1, R43.1, S2.3
MCLR2: C57.1, JP39.1, JP40.6, R55.1, R68.1, S3.3
MCLR3: C76.1, JP58.1, JP59.6, R80.1, R93.1, S4.3
MCLR4: C95.1, JP77.1, JP78.6, R105.1, R118.1, S5.3
MCLR5: C114.1, JP96.1, JP97.6, R130.1, R143.1, S6.3
MPU-CS: R25.1, TP1.P$1, U1.14
MPU-CS1: R50.1, TP5.P$1, U2.14
MPU-CS2: R75.1, TP9.P$1, U15.14
MPU-CS3: R100.1, TP13.P$1, U22.14
MPU-CS4: R125.1, TP17.P$1, U29.14
MPU-CS5: R150.1, TP21.P$1, U36.14
MPU-INT: U1.66, U10.12
MPU-INT1: U2.66, U14.12
MPU-INT2: U15.66, U21.12
MPU-INT3: U22.66, U28.12
MPU-INT4: U29.66, U35.12
MPU-INT5: U36.66, U42.12
MPU-MISO: TP3.P$1, U1.11, U10.9
MPU-MISO1: TP7.P$1, U2.11, U14.9
MPU-MISO2: TP11.P$1, U15.11, U21.9
MPU-MISO3: TP15.P$1, U22.11, U28.9
MPU-MISO4: TP19.P$1, U29.11, U35.9
MPU-MISO5: TP23.P$1, U36.11, U42.9
MPU-MOSI: TP4.P$1, U1.12, U10.24
MPU-MOSI1: TP8.P$1, U2.12, U14.24
MPU-MOSI2: TP12.P$1, U15.12, U21.24
MPU-MOSI3: TP16.P$1, U22.12, U28.24
MPU-MOSI4: TP20.P$1, U29.12, U35.24
MPU-MOSI5: TP24.P$1, U36.12, U42.24
MPU-SCK: TP2.P$1, U1.10, U10.23
MPU-SCK1: TP6.P$1, U2.10, U14.23
MPU-SCK2: TP10.P$1, U15.10, U21.23
MPU-SCK3: TP14.P$1, U22.10, U28.23
MPU-SCK4: TP18.P$1, U29.10, U35.23
MPU-SCK5: TP22.P$1, U36.10, U42.23
unnamed: R2.1, STAT1.A
unnamed: R4.1, STAT2.A
unnamed: U1.64, Y1.3
unnamed: C12.+, U6.2
unnamed: R25.2, U10.8
unnamed: U1.63, Y1.1
unnamed: R15.2, U1.13
unnamed: R26.1, STAT5.A
unnamed: R1.1, R8.2, U5.ADJ
unnamed: R27.1, STAT6.A
unnamed: R28.1, STAT7.A
unnamed: R29.1, STAT8.A
unnamed: C2.1, U10.20
unnamed: I8.3, R16.2
unnamed: I4.3, R17.2
unnamed: C9.1, U10.10
unnamed: I3.3, R18.2
unnamed: I7.3, R19.2
unnamed: I6.3, R20.2
unnamed: I2.3, R21.2
unnamed: I1.3, R22.2
unnamed: I10.3, R31.2
unnamed: I11.3, R32.2
unnamed: I12.3, R33.2
unnamed: I9.3, R34.2
unnamed: I14.3, R35.2
unnamed: I5.3, R23.2
unnamed: I15.3, R36.2
unnamed: I16.3, R37.2
unnamed: I13.3, R38.2
unnamed: C22.A, U2.85
unnamed: U2.64, Y2.3
unnamed: R10.1, STAT3.A
unnamed: R11.1, STAT4.A
unnamed: C28.A, U1.85
unnamed: U2.63, Y2.1
unnamed: R43.2, U2.13
unnamed: R44.1, R45.2, U7.ADJ
unnamed: C33.1, U14.20
unnamed: C34.1, U14.10
unnamed: C37.+, U11.2
unnamed: R50.2, U14.8
unnamed: R51.1, STAT9.A
unnamed: R52.1, STAT10.A
unnamed: R53.1, STAT11.A
unnamed: R54.1, STAT12.A
unnamed: I18.3, R56.2
unnamed: I19.3, R57.2
unnamed: I20.3, R58.2
unnamed: I17.3, R59.2
unnamed: I22.3, R60.2
unnamed: I23.3, R61.2
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

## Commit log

2013-01-25 adding files
    [UDB5-v010.brd, UDB5-v010.sch]
2013-01-28 prototype v010
    added gerbers
    [UDB5-v010.brd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]
2013-01-28 added bom
2013-01-28 Deleted gerbers
    [UDB5-v010.GBL, UDB5-v010.GBO, UDB5-v010.GBS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]
2013-03-12 v011
    -swapped MPU MOSI and MISO, labeled them correctly.
    -increased silk txt on PCB
    [UDB5.brd, UDB5.sch]
2013-04-26 v10
    red board order
    [UDB5.brd]
2013-04-26 v10
    -added readmes
    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
2013-05-02 v10 red boards
    production red boards
    [UDB5.brd, UDB5.sch]
2013-05-02 Production files
    created panel for production
    [UDB5-Panel-v10.brd]

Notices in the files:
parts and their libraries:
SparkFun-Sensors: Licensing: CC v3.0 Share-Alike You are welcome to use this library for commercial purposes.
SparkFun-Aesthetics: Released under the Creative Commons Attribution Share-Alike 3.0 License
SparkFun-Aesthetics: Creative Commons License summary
